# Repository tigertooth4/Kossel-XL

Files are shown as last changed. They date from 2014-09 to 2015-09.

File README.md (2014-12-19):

Kossel-XL
=========

Yet another large Kossel 3D printer using 20x20 aluminum extrusion, different from KosselXL (http://www.builda3dprinter.eu/kosselxl-released/)
XL means both "extra-large" and the abbreviation of my chinese name ;-)

For the look of it, please see the following pics:
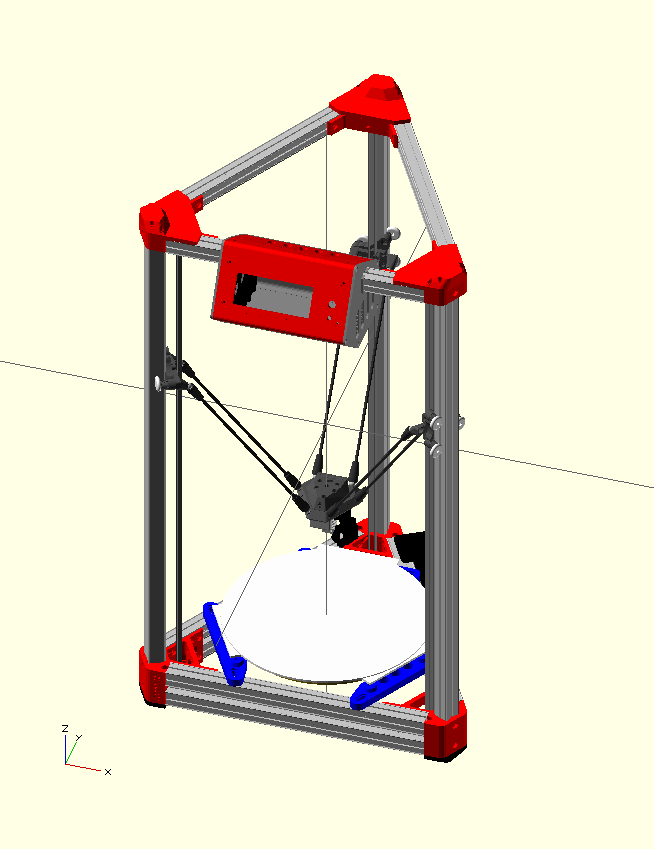
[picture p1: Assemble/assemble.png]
assemble

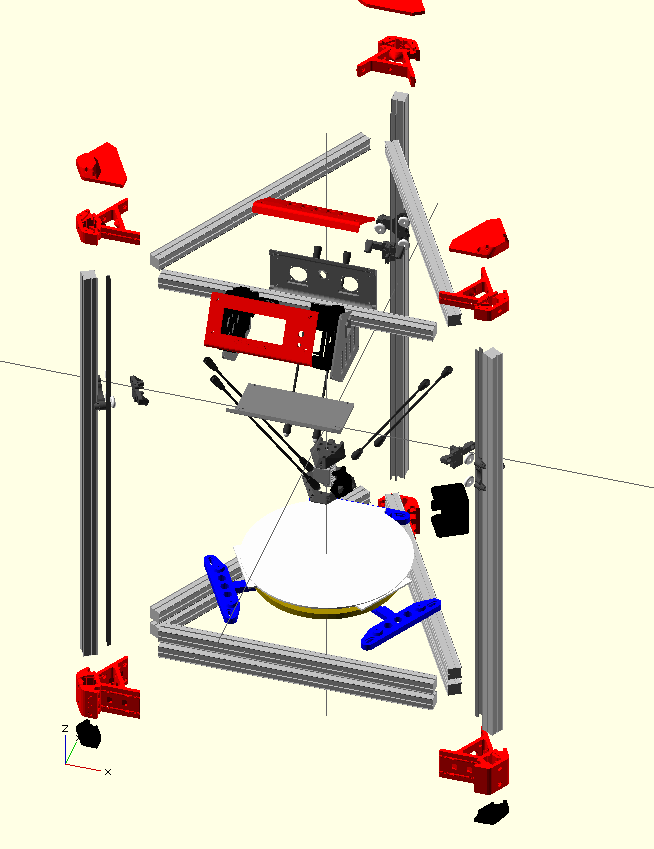
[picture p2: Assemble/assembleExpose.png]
assemble


Having known there are different implementations scattering around, but most of them did not give a complete set of files and designs, I decided to make my own Kossel 3D printer (see Reprap.org for further info about Kossel 3D printer). To me the goal is very clear: I want to build a Kossel with the follow features:

- larger print volumn than usual Kossel (I'm using 20x20 aluminum extrusion with the bottom edge = 330mm and height = 700mm)
- large print area ( almost the same as a standard Prusa i3 )
- magenetic ball joints 
- lighter carriages sliding on the aluminum extrusion directly
- probeless auto-levelling (Using the hotend itself or a proximation sensor)
- high precision at a reasonable speed
- heated bed 
- easy to assemble and maintain 

All the printed parts are implemented in OpenSCAD by myself! (But of course they are based on the original design of Kossel and other Kossel-type 3DPs such as Atom3DP etc.).

## Caution

This is a project in its very early stage. I'm still tweaking the design a lot. So using at your own risk!

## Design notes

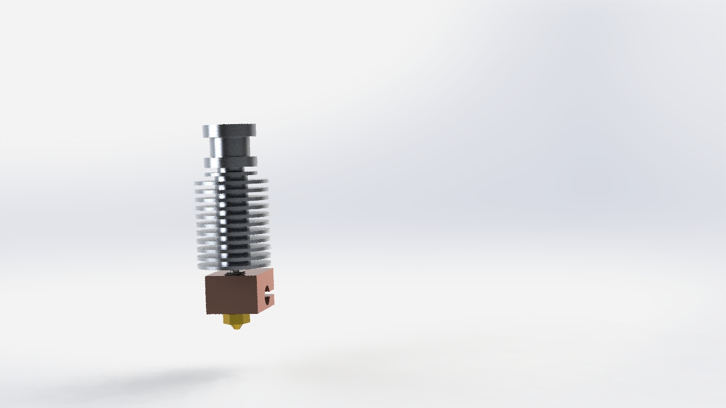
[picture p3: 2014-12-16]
Effector-new/e3d-v6-1-75-hotend-1/Renderings/preview4.JPG

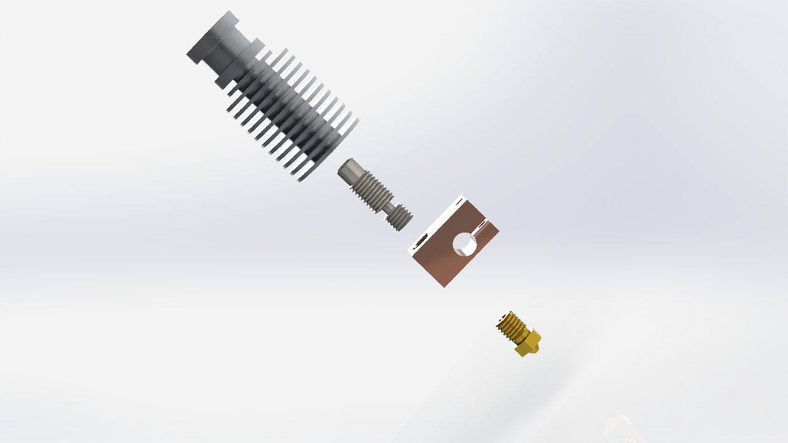
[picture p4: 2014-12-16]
Effector-new/e3d-v6-1-75-hotend-1/Renderings/preview2.JPG

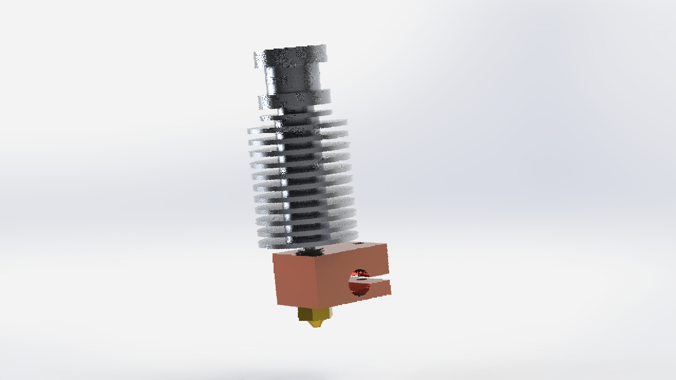
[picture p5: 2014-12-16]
Effector-new/e3d-v6-1-75-hotend-1/Renderings/preview3.JPG

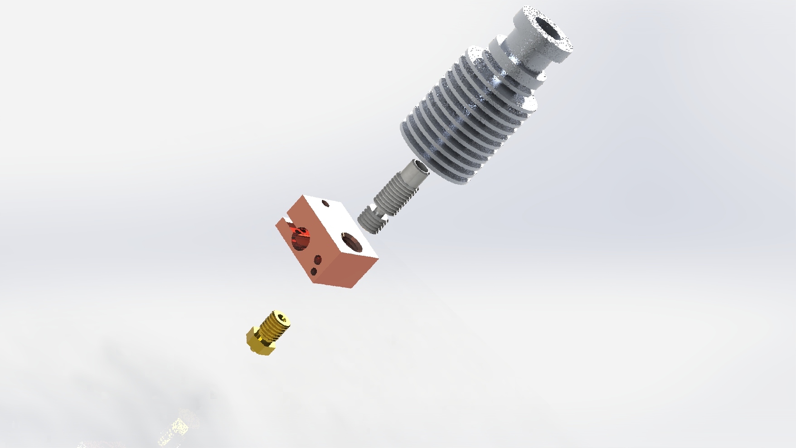
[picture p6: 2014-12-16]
Effector-new/e3d-v6-1-75-hotend-1/Renderings/preview.JPG

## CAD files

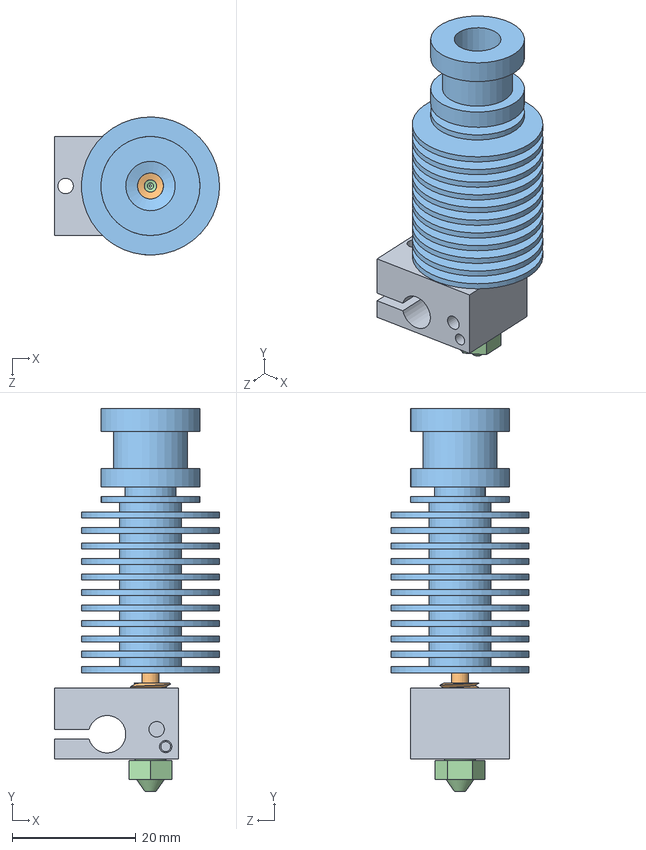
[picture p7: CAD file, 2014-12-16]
Effector-new/e3d-v6-1-75-hotend-1/E3D V6 1.75 Uni model.SLDASM
26.6 x 61.9 x 22.3 mm
V6-BLOCK
V6-175-BREAK
V6-175-SINK
V6-NOZZLE-175-035

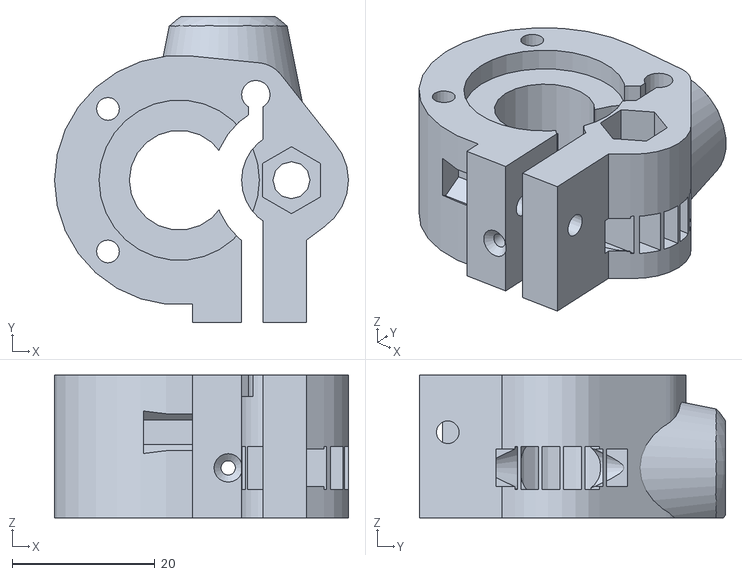
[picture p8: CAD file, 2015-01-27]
BowdenExtruder/kosselExtruder-new.stl
41.2 x 43.0 x 20.0

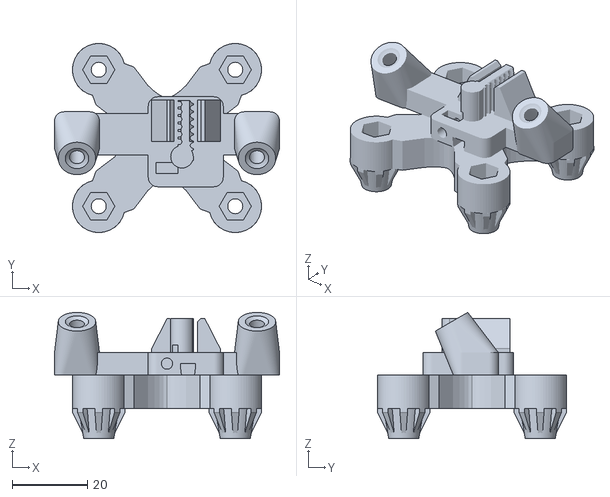
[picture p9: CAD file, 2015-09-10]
Carriage-v2/X-carriage-new.stl
60.0 x 50.4 x 33.7

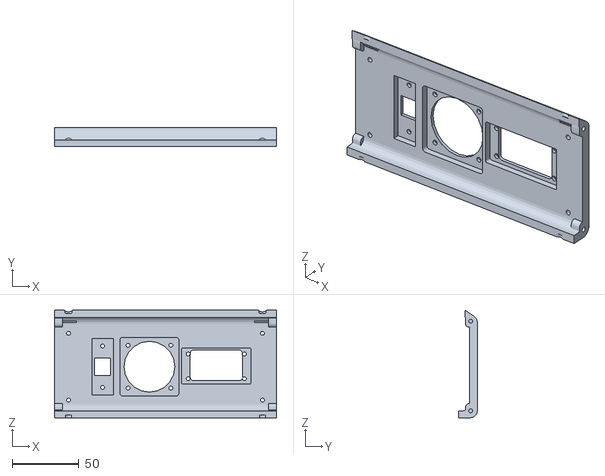
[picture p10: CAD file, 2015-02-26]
Case/rampsBackFaceNew_v3.stl
166.0 x 14.0 x 80.6

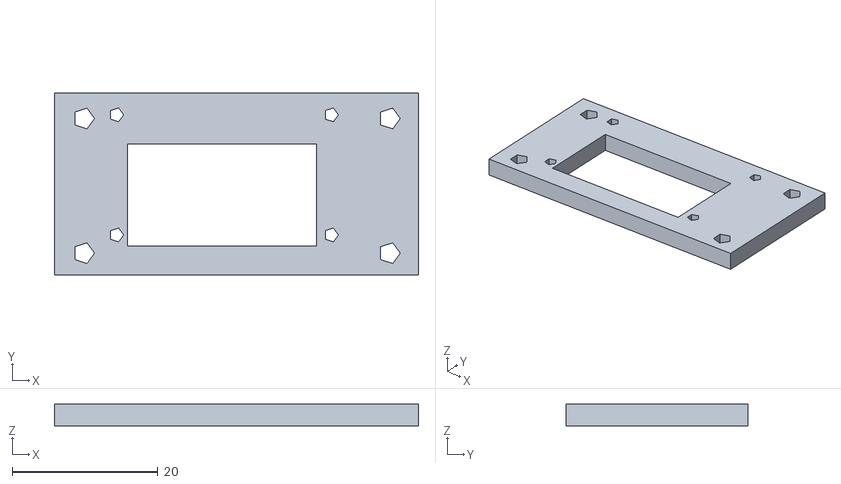
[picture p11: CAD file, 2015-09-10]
CircuitCover/circuitCover.stl
50.0 x 25.0 x 3.00

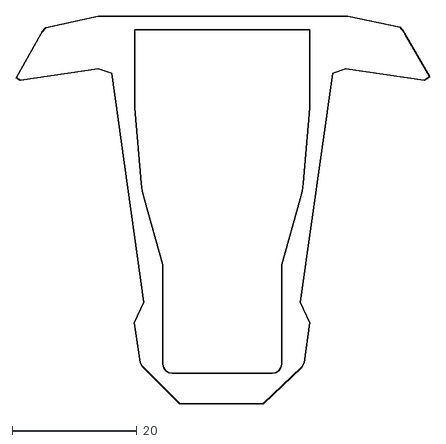
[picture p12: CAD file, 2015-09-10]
Effector-new/circuitboard-profile.dxf
66.3 x 62.0

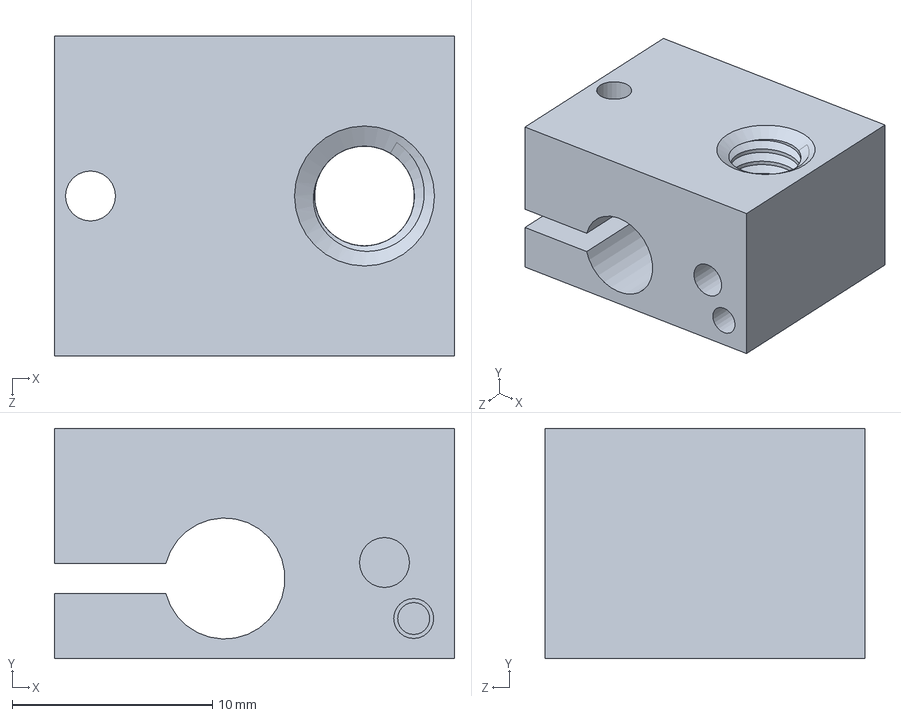
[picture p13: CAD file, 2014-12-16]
Effector-new/e3d-v6-1-75-hotend-1/V6-BLOCK.SLDPRT
20.0 x 11.5 x 16.0 mm

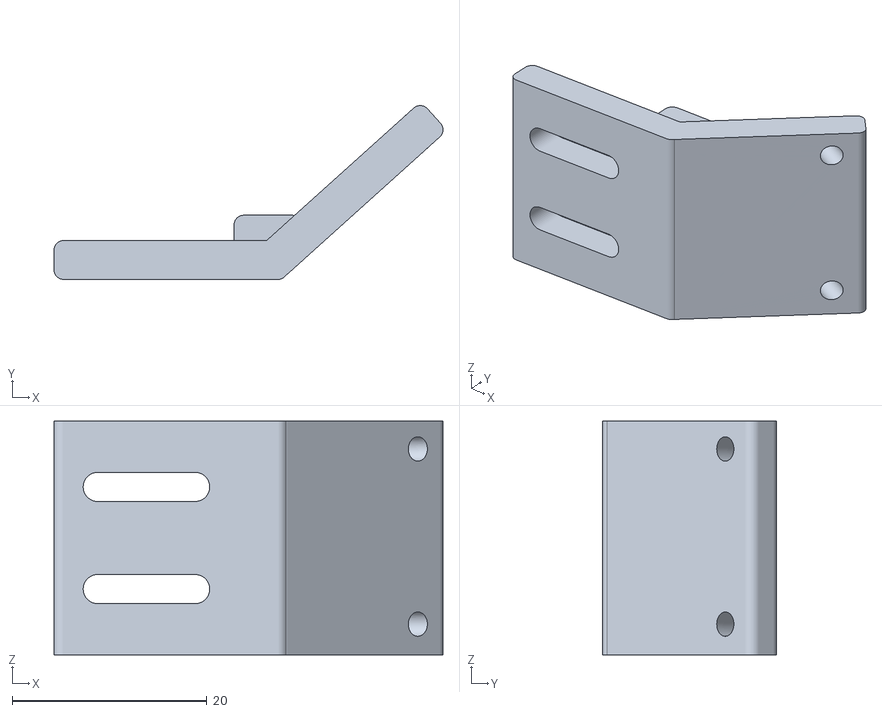
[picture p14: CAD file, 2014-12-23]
Effector/ProxMount2.stl
40.0 x 17.9 x 24.0

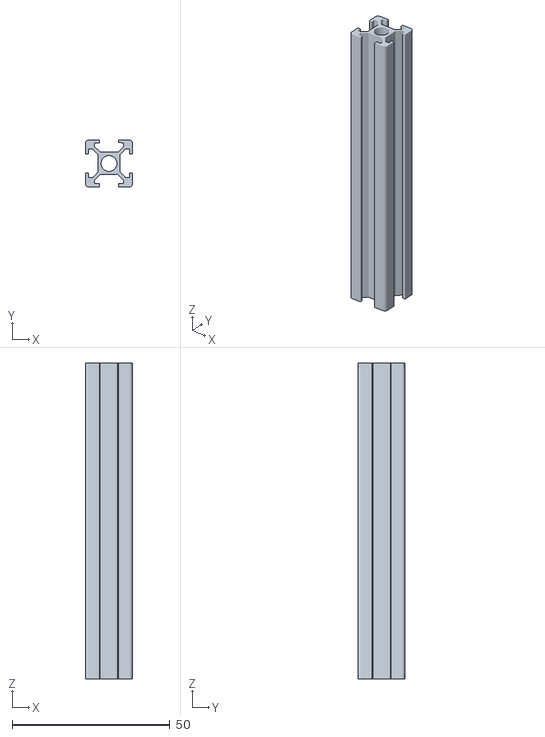
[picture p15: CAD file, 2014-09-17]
Extrusion/1515.stl
14.9 x 14.9 x 100.0

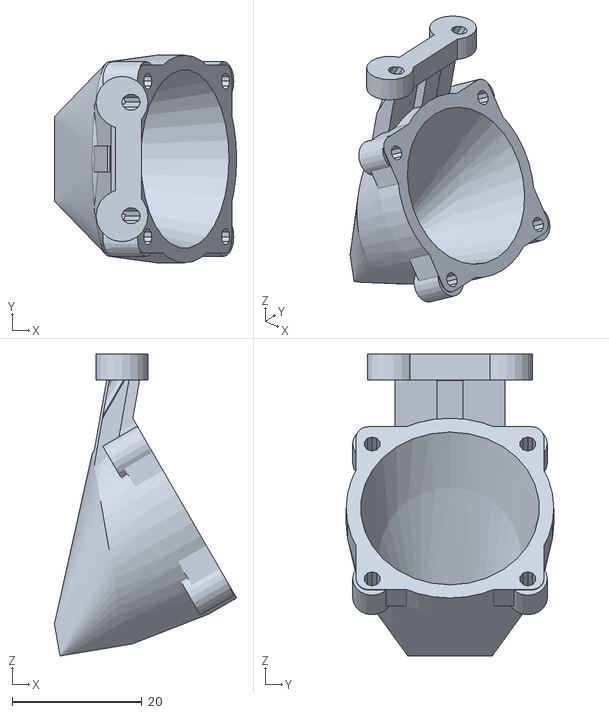
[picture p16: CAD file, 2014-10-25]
Fans/printFan-new.stl
28.1 x 32.0 x 46.5

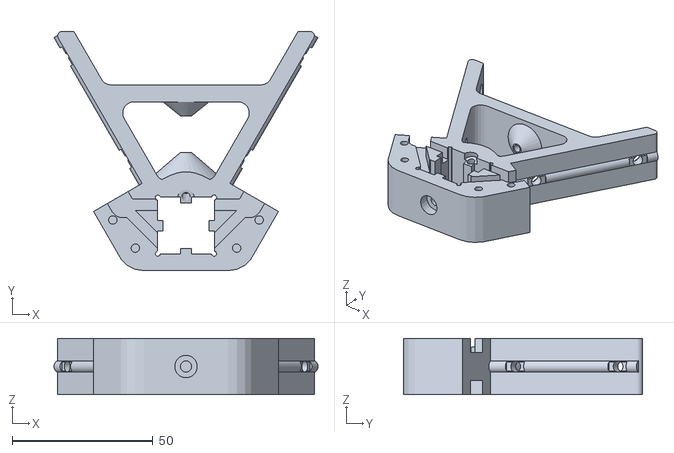
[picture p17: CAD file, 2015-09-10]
Frame/frameTop.stl
93.8 x 85.0 x 20.0

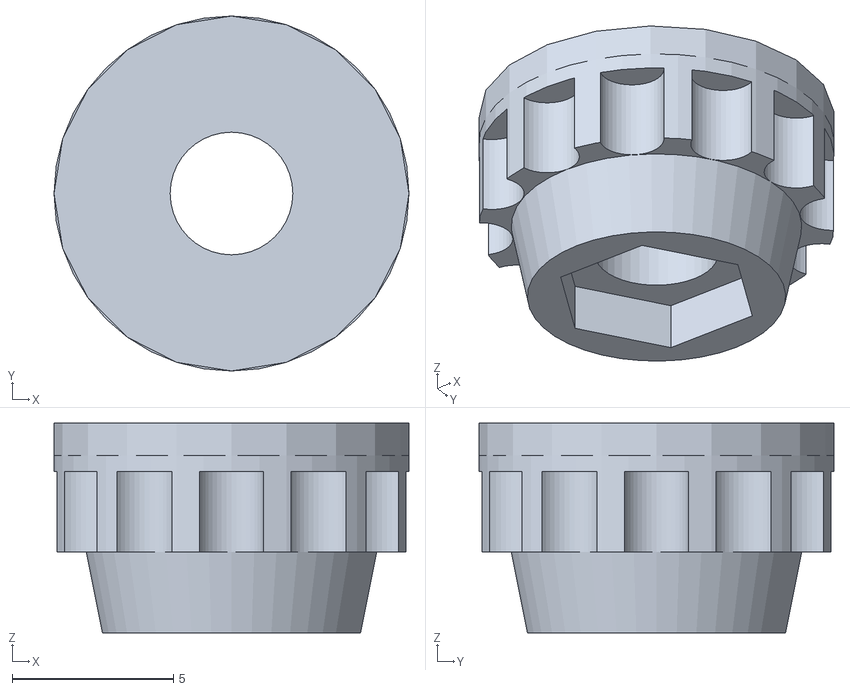
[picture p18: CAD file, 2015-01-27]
HeatbedSupport/TuneButton.stl
11.0 x 11.0 x 6.50

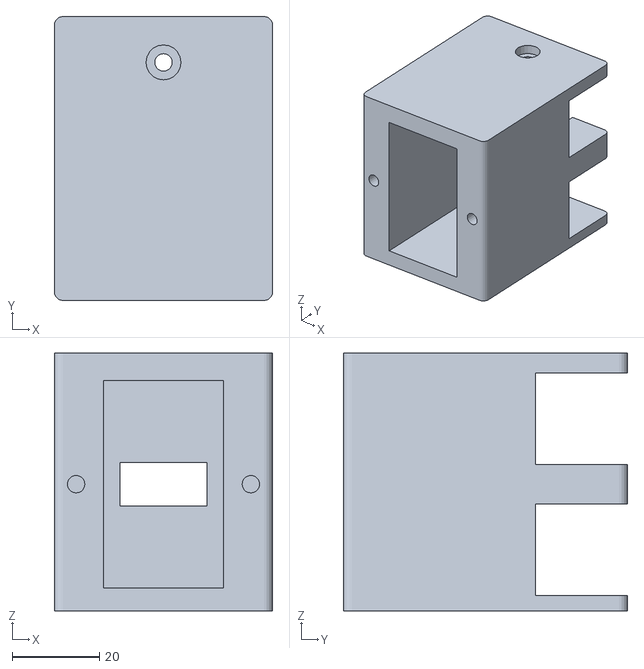
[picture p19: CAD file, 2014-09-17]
PowerBox/powerBox.stl
50.0 x 65.0 x 59.0

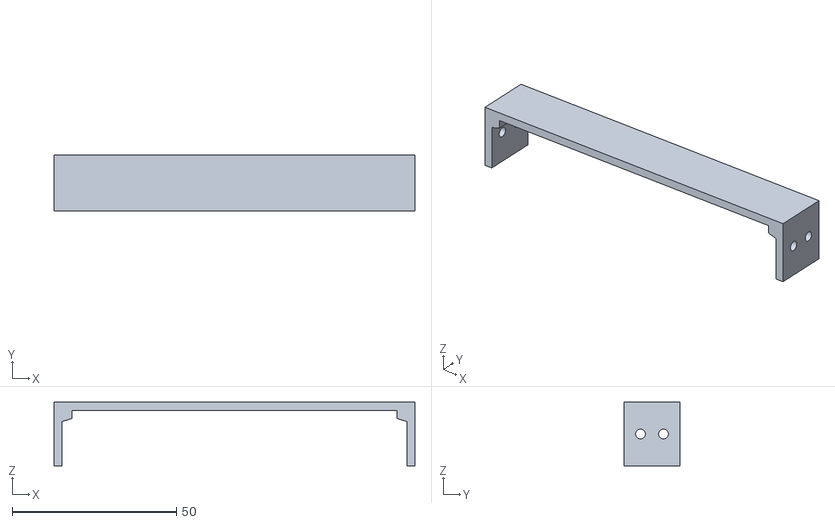
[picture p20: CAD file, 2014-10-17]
PowerBrickMount/powerCordCover.stl
110.0 x 17.0 x 19.5

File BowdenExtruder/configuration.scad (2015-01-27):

// Increase this if your slicer or printer make holes too tight.
extra_radius = 0.1;

// OD = outside diameter, corner to corner.
m3_nut_od = 6.1;
m3_nut_radius = m3_nut_od/2 + 0.2 + extra_radius;
m3_washer_radius = 3.5 + extra_radius;

// Major diameter of metric 3mm thread.
m3_major = 2.85;
m3_radius = m3_major/2 + extra_radius;
m3_wide_radius = m3_major/2 + extra_radius + 0.2;

// NEMA17 stepper motors.
motor_shaft_diameter = 5;
motor_shaft_radius = motor_shaft_diameter/2 + extra_radius;

// Frame brackets. M3x8mm screws work best with 3.6 mm brackets.
thickness = 3.6;

// OpenBeam or Misumi. Currently only 15x15 mm, but there is a plan
// to make models more parametric and allow 20x20 mm in the future.
extrusion = 15;

// Placement for the NEMA17 stepper motors.
motor_offset = 44;
motor_length = 47;

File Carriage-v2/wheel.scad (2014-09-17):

$fn = 60;

err = 0.1;
module wheel(r, holeRadius, thick){
	deducedRadius = r - thick/2;
	difference(){
		union(){
			rotate_extrude(convexity = 30){ translate([deducedRadius, 0, 0]) circle(r = thick/2, center=true); }	
			translate([0,0,-thick/2])	cylinder(r=deducedRadius, h = thick);
	}

	translate([0,0, -thick/2-err]) cylinder(r=holeRadius, h=thick+2*err);
}}

wheel(9.5,2,5);

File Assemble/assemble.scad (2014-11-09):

use <../Frame/frame.scad>
/*use <../Carriage/Y-carriage.scad>
use <../Case/RampsCase.scad>
use <../Effector/effector.scad>
use <../PowerBox/powerBox.scad>
use <../Rods/rod_connector.scad>
use <../Fans/fans.scad>
use <../HeatbedSupport/heatbedSupport.scad>*/
use <../PowerBrickMount/powerBrickMount.scad>


expose = 0;
l = 330 +expose;
r = l/2+110 + expose;
h = 700;
extrusion = 20;

translate([0,0,-h/2]){

// draw the motor frame
for(i=[0,120,240])
rotate([0,0,i])
translate([-r*cos(30),-r*sin(30),0])rotate([0,0, -60])
translate([0,80,-expose])
{
    color("red") import("../Frame/frameMotor.stl");
    color("black")translate([0,0,22-expose/2]) import("../Frame/bottomCover.stl");
}

// draw the top frame

for(i=[0,120,240])
rotate([0,0,i])
translate([-r*cos(30),-r*sin(30),0])rotate([0,0, -60])
translate([0,80,h-10+expose])
{
    color("red")import("../Frame/frameTop.stl");
    color("red")translate([0,0,-1+expose]) import("../Frame/topCover.stl");
}

// draw the bottom aluminum
color("silver")
for(i=[0,120,240])
rotate([0,0,i])
for(z=[extrusion/2+5,-extrusion/2-5])
translate([0,-(l/2+80)*cos(60),z])rotate([0,90,0])extrusion(l);

// draw the top aluminum
color("silver")
for(i=[0,120,240])
rotate([0,0,i])
translate([0,-(l/2+80)*cos(60),h-10])rotate([0,90,0])extrusion(l);

// draw the vertical aluminum
color("silver")
for(i=[0,120,240])
rotate([0,0,i+30])
translate([-r+60, 0,h/2-10]) extrusion(h+20);

// draw the y-carriage
for(i=[0,120,240])
rotate([0,0,i])
translate([0,r-75,h/3*2])rotate([90,0,0]){
    color([0.3,0.3,0.3])translate([6,0,expose/2])import("../Carriage/wing.stl");
    color([0.3,0.3,0.3])import("../Carriage/Ycarriage.stl");

    color("white")translate([5,0,0])for(i=[0,120,240])rotate([0,0,i])translate([-25,0,-16 + expose/3])
    import("../Carriage/wheel.stl");
}

// draw the belts
color("grey")
for(i=[0,120,240])
rotate([0,0,i+30])
translate([-r+90, 0,h/2-10]) {
    for(y=[-4,4])
    translate([0,y,0])
    cube([6,1.5,h],center=true);
}

// draw the cases
translate([0,-l*cos(60)+55,h-30]){
    color("black"){
	translate([0,-expose/2,expose/2])import("../Case/skeletonSideR.stl");
	translate([0,-expose/2,expose/2])import("../Case/skeletonSideL.stl");
	for(x=[-40,40])
	translate([x,45-expose/2,expose/2-30])rotate([-90,0,0])import("../Case/rampsFan.stl");
    }
    
    color("red") {
	translate([0,-expose,expose])import("../Case/rampsLcdFace.stl");
	translate([0,expose,expose])import("../Case/rampsTopFace.stl");
    }

    color("grey"){
	import("../Case/rampsLeftFace.stl");
	import("../Case/rampsRightFace.stl");
	
	translate([0,expose,0])import("../Case/rampsBackFace.stl");
	translate([0,0,-expose])import("../Case/rampsBottomFace.stl");


    }
}


// draw the effector
translate([0,0, h/3])
rotate([0,0,30])
{
    color([0.3,0.3,0.3])rotate([0,0,-120]) import("../Effector/base.stl");
    color([0.3,0.3,0.3])rotate([0,0,-120]) translate([0,0,  expose/2]) import("../Effector/lid.stl");
    rotate([0,0,60]){
	//color("silver") translate([0,0,expose/2])import("../Fans/hotend.stl"); color("silver")
	color("silver")translate([0,0,expose/2+2]) rotate([0,0,-90])import("../E3D_v4_Hot_end_Model/E3Dhotend.stl");
	//color("black") translate([0,0,expose/2])rotate([0,0,-110])import("../Fans/hotendFan.stl");
	color("black") translate([0,0,expose/2])rotate([0,0,-120])translate([7,0,0])import("../Fans/printFan.stl");
    }
}

//draw the rod

translate([0,0,h/3+30+expose/2])
for(i=[0,120,240])
rotate([0,34,-30+i])
for(y=[-23,23])
translate([38,y+expose/2,0])
{
    color([0.2,0.2,0.2])
    {
	translate([0,0,255+expose/4])import("../Rods/rod_connector.stl");
	translate([0,0,expose/4])cylinder(r=2,h=260);
	translate([0,0,5])rotate([180,0,0])import("../Rods/rod_connector.stl");
    }
    translate([0,0,262]) color("silver") sphere(r=4, $fn=30, center=true);
    translate([0,0,-2])color("silver") sphere(r=4,$fn=30,center=true);

}

// draw the power box
color("black")translate([l*cos(60)-100,l*sin(60)-90,0])
rotate([0,0,120])
{
    import("../PowerBox/powerBoxRight.stl");
    import("../PowerBox/powerBoxLeft.stl");
}

// draw the heatbed support
translate([0,0,30+expose/3]){
    color("grey") translate([0,0,-5])rotate([0,0,30])import("../HeatbedSupport/centerSupport.stl");
    color("blue") for(i=[0,120,240])rotate([0,0,60+i])translate([0,-130-expose/3,0])
    import("../HeatbedSupport/hbsupport.stl");
}


// draw the plate
color([0.65,0.55,0]) translate([0,0,35+expose/3])
cylinder(r=114.3 , h=10, $fn=60);
color([0.98,0.98,0.98]) translate([0,0, 50+expose/2])
union(){
    cylinder(r=130, h =3, $fn=60);
    for(i=[0,120,240]) rotate([0,0,-30+i])
    translate([125,0,0])minkowski(){
	cube([13,100,2],center=true);
	cylinder(r=1,h=1,center=true,$fn=20);}
}

// draw the power brick and mounts
color("silver") cube([113,215,45],center=true);
color("black") {
translate([-113/2+32,215/2-32,-30-expose/2])rotate([0,0,-30])mount(68);
translate([-113/2+32,-215/2+32,-30-expose/2]) rotate([0,0,90]) mount(45);

translate([113/2-32,215/2-32,-30-expose/2])rotate([0,0,-150])mount(68);
translate([113/2-32,-215/2+32,-30-expose/2]) rotate([0,0,90]) mount(45);

}

// draw the romote bowden extruder mount
color([0.1, 0.1, 0.1])translate([122,0, h-40+expose])rotate([90,0,-60]) import("../BowdenExtruder/extruderMount.stl");
color([0.1, 0.1, 0.1])translate([85,-25, h-40+expose]) rotate([-90,0,-60])import("../BowdenExtruder/extruder_with_metal_nut_place_to_hold_bowden_tube.stl");

}

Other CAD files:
References/Kossel-Extrusion-2020/2020.stl
References/mk_visual_calc2020/carriage.stl
Rods/rod_connector-new.stl
Tension/Tensioner.stl
BowdenExtruder/ExtruderKai-modify.scad
BowdenExtruder/ExtruderKai-modify.stl
BowdenExtruder/extruderMount.scad
BowdenExtruder/extruderMount.stl
BowdenExtruder/extruder_with_metal_nut_place_to_hold_bowden_tube.stl
BowdenExtruder/kosselExtruder-new.scad
Carriage-v2/X-carriage-back.stl
Carriage-v2/X-carriage-new.scad
Carriage-v2/anotherEnd.stl
Carriage-v2/roundedBox.scad
Carriage/Y-carriage-deprecated.scad
Carriage/Y-carriage-new-but-not-useful.scad
Carriage/Y-carriage-new.scad
Carriage/Y-carriage-new.stl
Carriage/Y-carriage-slim-deprecated.scad
Carriage/Y-carriage.scad
Carriage/Ycarriage.stl
Carriage/anotherEnd.stl
Carriage/wheel.stl
Carriage/wing.stl
Case/RampsCase.scad
Case/RampsCaseNew.scad
Case/SDcardProlong.scad
Case/SDcardProlong.stl
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

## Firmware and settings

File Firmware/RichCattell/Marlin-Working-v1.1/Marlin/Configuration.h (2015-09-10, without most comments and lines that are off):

#define CONFIGURATION_H
#define STRING_VERSION_CONFIG_H __DATE__ " " __TIME__ // build date and time
#define STRING_CONFIG_H_AUTHOR "(XJ Liu, Kossel XL)" // Who made the changes.
#define SERIAL_PORT 0
#define BAUDRATE 115200
#define MOTHERBOARD 33
#define CUSTOM_MENDEL_NAME "Kossel XL"
#define EXTRUDERS 1
#define POWER_SUPPLY 1
#define DELTA
#define DELTA_SEGMENTS_PER_SECOND 200
#define DEFAULT_DELTA_DIAGONAL_ROD 280.2 // mm
#define DELTA_SMOOTH_ROD_OFFSET  216.69 // 216.17 // mm //158
#define DELTA_EFFECTOR_OFFSET 30.30 // mm
#define DELTA_CARRIAGE_OFFSET 39.04 // mm
#define DEFAULT_DELTA_RADIUS (DELTA_SMOOTH_ROD_OFFSET-DELTA_EFFECTOR_OFFSET-DELTA_CARRIAGE_OFFSET)
#define AUTOCALIBRATION_PRECISION 0.03 // mm
#define BED_DIAMETER 160 // mm
#define Z_PROBE_OFFSET {0,-22.9, 1.3, 0}//{-30, -17, -0.45, 0}  // X, Y, Z, E distance between hotend nozzle and deployed bed leveling probe.
#define Z_PROBE_DEPLOY_START_LOCATION {0, 0, 10, 0}   // X, Y, Z, E start location for z-probe deployment sequence
#define Z_PROBE_DEPLOY_END_LOCATION {0, 0, 10, 0} 	  // X, Y, Z, E end location for z-probe deployment sequence
#define Z_PROBE_RETRACT_START_LOCATION {0, 0, 5, 0}  // X, Y, Z, E start location for z-probe retract sequence
#define Z_PROBE_RETRACT_END_LOCATION {0, 0, 2.5, 0}     // X, Y, Z, E end location for z-probe retract sequence
#define AUTOLEVEL_GRID 24 // Distance between autolevel Z probing points, should be less than print surface radius/3.
#define TEMP_SENSOR_0 1
#define TEMP_SENSOR_1 0
#define TEMP_SENSOR_2 0
#define TEMP_SENSOR_BED 1
#define MAX_REDUNDANT_TEMP_SENSOR_DIFF 10
#define TEMP_RESIDENCY_TIME 10  // (seconds)
#define TEMP_HYSTERESIS 3       // (degC) range of +/- temperatures considered "close" to the target one
#define TEMP_WINDOW     1       // (degC) Window around target to start the residency timer x degC early.
#define HEATER_0_MINTEMP 5
#define HEATER_1_MINTEMP 5
#define HEATER_2_MINTEMP 5
#define BED_MINTEMP 5
#define HEATER_0_MAXTEMP 275
#define HEATER_1_MAXTEMP 275
#define HEATER_2_MAXTEMP 275
#define BED_MAXTEMP 150
#define PIDTEMP
#define BANG_MAX 255 // limits current to nozzle while in bang-bang mode; 255=full current
#define PID_MAX 255 // limits current to nozzle while PID is active (see PID_FUNCTIONAL_RANGE below); 255=full current
  #define PID_FUNCTIONAL_RANGE 10 // If the temperature difference between the target temperature and the actual temperature
  #define PID_INTEGRAL_DRIVE_MAX 255  //limit for the integral term
  #define K1 0.95 //smoothing factor within the PID
  #define PID_dT ((16.0 * 8.0)/(F_CPU / 64.0 / 256.0)) //sampling period of the temperature routine
    #define  DEFAULT_Kp 18.73 // For MK2 20.73
    #define  DEFAULT_Ki 1.58  // For MK2 1.35
    #define  DEFAULT_Kd 55.53 // For MK2 79.81
#define MAX_BED_POWER 255 // limits duty cycle to bed; 255=full current
#define PREVENT_DANGEROUS_EXTRUDE
#define PREVENT_LENGTHY_EXTRUDE
#define EXTRUDE_MINTEMP 190
#define EXTRUDE_MAXLENGTH (X_MAX_LENGTH+Y_MAX_LENGTH) //prevent extrusion of very large distances.
#define ENDSTOPPULLUPS // Comment this out (using // at the start of the line) to disable the endstop pullup resistors
  #define ENDSTOPPULLUP_XMAX
  #define ENDSTOPPULLUP_YMAX
  #define ENDSTOPPULLUP_ZMAX
  #define ENDSTOPPULLUP_XMIN
  #define ENDSTOPPULLUP_YMIN
  #define ENDSTOPPULLUP_ZMIN
const bool X_MIN_ENDSTOP_INVERTING = false; // set to true to invert the logic of the endstop.
const bool Y_MIN_ENDSTOP_INVERTING = false; // set to true to invert the logic of the endstop.
const bool Z_MIN_ENDSTOP_INVERTING = true; //false for MK2 ; // set to true to invert the logic of the endstop.
const bool X_MAX_ENDSTOP_INVERTING = false; // set to true to invert the logic of the endstop.
const bool Y_MAX_ENDSTOP_INVERTING = false; // set to true to invert the logic of the endstop.
const bool Z_MAX_ENDSTOP_INVERTING = false; // set to true to invert the logic of the endstop.
#if defined(COREXY) && !defined(DISABLE_MAX_ENDSTOPS)
  #define DISABLE_MAX_ENDSTOPS
#endif
#define X_ENABLE_ON 0
#define Y_ENABLE_ON 0
#define Z_ENABLE_ON 0
#define E_ENABLE_ON 0 // For all extruders
#define DISABLE_X false
#define DISABLE_Y false
#define DISABLE_Z false
#define DISABLE_E false // For all extruders
#define INVERT_X_DIR false    // for Mendel set to false, for Orca set to true
#define INVERT_Y_DIR false    // for Mendel set to true, for Orca set to false
#define INVERT_Z_DIR false    // for Mendel set to false, for Orca set to true
#define INVERT_E0_DIR false   // for direct drive extruder v9 set to true, for geared extruder set to false
#define INVERT_E1_DIR false   // for direct drive extruder v9 set to true, for geared extruder set to false
#define INVERT_E2_DIR false   // for direct drive extruder v9 set to true, for geared extruder set to false
#define X_HOME_DIR 1
#define Y_HOME_DIR 1
#define Z_HOME_DIR 1
#define min_software_endstops true // If true, axis won't move to coordinates less than HOME_POS.
#define max_software_endstops true  // If true, axis won't move to coordinates greater than the defined lengths below.
#define X_MAX_POS 130
#define X_MIN_POS -130
#define Y_MAX_POS 130
#define Y_MIN_POS -130
#define Z_MAX_POS MANUAL_Z_HOME_POS
#define Z_MIN_POS 0
#define X_MAX_LENGTH (X_MAX_POS - X_MIN_POS)
#define Y_MAX_LENGTH (Y_MAX_POS - Y_MIN_POS)
#define Z_MAX_LENGTH (Z_MAX_POS - Z_MIN_POS)
#define MANUAL_HOME_POSITIONS  // If defined, MANUAL_*_HOME_POS below will be used
#define BED_CENTER_AT_0_0  // If defined, the center of the bed is at (X=0, Y=0)
#define MANUAL_X_HOME_POS 0
#define MANUAL_Y_HOME_POS 0
#define MANUAL_Z_HOME_POS 265.35 //for MK2 238  // For delta: Distance between nozzle and print surface after homing.
#define NUM_AXIS 4 // The axis order in all axis related arrays is X, Y, Z, E
#define HOMING_FEEDRATE {70*60, 70*60, 70*60, 0}  // set the homing speeds (mm/min)
#define DEFAULT_AXIS_STEPS_PER_UNIT   {200, 200, 200, 469.4}
#define DEFAULT_MAX_FEEDRATE          {200, 200, 200, 200}    // (mm/sec)
#define DEFAULT_MAX_ACCELERATION      {3000, 3000, 3000, 3000} // Never set this too high {9000,9000,9000,9000}    // X, Y, Z, E maximum start speed for accelerated moves. E default values are good for skeinforge 40+, for older versions raise them a lot.
#define DEFAULT_ACCELERATION          1000 //3000    // X, Y, Z and E max acceleration in mm/s^2 for printing moves
#define DEFAULT_RETRACT_ACCELERATION  1500 //3000   // X, Y, Z and E max acceleration in mm/s^2 for retracts
#define DEFAULT_XYJERK                20.0    // (mm/sec)
#define DEFAULT_ZJERK                 20.0    // (mm/sec)
#define DEFAULT_EJERK                 20.0    // (mm/sec)
#define EEPROM_SETTINGS
#define EEPROM_CHITCHAT
#define PLA_PREHEAT_HOTEND_TEMP 180
#define PLA_PREHEAT_HPB_TEMP 60
#define PLA_PREHEAT_FAN_SPEED 255   // Insert Value between 0 and 255
#define ABS_PREHEAT_HOTEND_TEMP 240
#define ABS_PREHEAT_HPB_TEMP 90
#define ABS_PREHEAT_FAN_SPEED 255   // Insert Value between 0 and 255
#define SDSUPPORT // Enable SD Card Support in Hardware Console
#define REPRAP_DISCOUNT_SMART_CONTROLLER
 #define ULTIPANEL
 #define NEWPANEL
  #define SDSUPPORT
  #define ULTRA_LCD
    #define LCD_WIDTH 20
    #define LCD_HEIGHT 4
#define SOFT_PWM_SCALE 0
#include "Configuration_adv.h"
#include "thermistortables.h"

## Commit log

2014-09-17 Initial submit, this is a project of my own. WIP.
    [1515.stl, 2020.stl, 2020_1000mm.stl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]
2014-09-24 An assemble file added
    [HeatbedSupport.scad, RampsCase.scad, Y-carriage.scad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]
2014-09-25 Assembled pics updated
    [.#effector.scad, RampsCase.scad, assemble.scad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]
2014-09-25 assemble pic updated again!
    [.#effector.scad, 2020_1000mm.stl, Orbitron_Medium.scad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]
2014-09-30 Modified the size of heatbad support
    [HeatbedSupport.scad, assemble.scad, centerSupport.stl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]
2014-10-17 Modified extruder fans and carriage(see Y-carriage-new.scad)
    [HeatbedSupport.scad, Tensioner.scad, Tensioner.stl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]
2014-10-18 Modified print fan and belt Clipper design, make it stronger
    [Y-carriage-new.scad, anotherEnd.stl, fans.scad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]
2014-10-25 I forgot what I've changed
    [E3D_hot_end.scad, E3Dhotend.stl, assemble.scad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]
2014-11-07 Drew the top covers of the top frame
    [SDcardProlong.scad, SDcardProlong.stl, TuneButton.scad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]
2014-11-09 Modified the top covers
    [assemble.scad, frame.scad, topCover.stl]
2014-12-03 modifed ramps back cover design, start a new effector design to use Fotek proximate sensor
    [50x50mm.stl, ProxMount.stl, RampsCase.scad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]
2014-12-16 updated rod design
    [E3D V6 1.75 Uni model - V6-175-BREAK-1.STL, E3D V6 1.75 Uni model - V6-175-SINK-1.STL, E3D V6 1.75 Uni model - V6-BLOCK-1.STL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]
2014-12-19 modified proximation sensor mount
    [effector.scad]
2014-12-23 Marlin firmware added
    [Configuration.h, Configuration_adv.h, Menu Plans.xlsx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]
2014-12-24 Found two possible bugs in G30 RichCattel's Marlin firmware
2014-12-26 Re-indented marlin_main.cpp
2015-01-27 Modified the bowden extruder design
    [Configuration.h, Configuration_adv.h, Menu Plans.xlsx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]
2015-02-04 Designing a new effector for better integration of blowing fans and heat sink fans
    [effectorNew.scad, upperLayer.stl]
2015-02-08 Updating the new effector for better integration of blowing fans and heat sink fans
    [effectorNew.scad]
2015-02-13 Thinking of adding a waved washer inside the Heatsink mount as an oscillation avoider
    [E3D_hot_end.scad, E3Dhotend.stl, e3d-hotend-V5.scad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]
2015-02-26 Finished new effector design.
    [Configuration.h, Configuration_adv.h, Menu Plans.xlsx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]
2015-02-26 Updated effectorNew's stl file
    [effectorLower.stl, effectorNew.scad, effectorUpper.stl]
2015-09-10 Carriage updated to v2
    [Configuration.h, Configuration_adv.h, E3D V6 1.75 Uni model - V6-175-BREAK-1.STL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]
